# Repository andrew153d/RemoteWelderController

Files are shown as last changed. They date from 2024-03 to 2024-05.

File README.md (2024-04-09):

# RemoteWelderController #

A pair of devices meant to retrofit older welders with wireless connectivity. This document covers the usage and mechanical makeup, the cost overview can be found [here](https://github.com/andrew153d/RemoteWelderController/tree/main/hardware). There is also a preview of the site at this [link](https://andrew153d.github.io/RemoteWelderController/firmware/webpage/web_controller.html), note functionality is limited.

--- 

<p align="center">
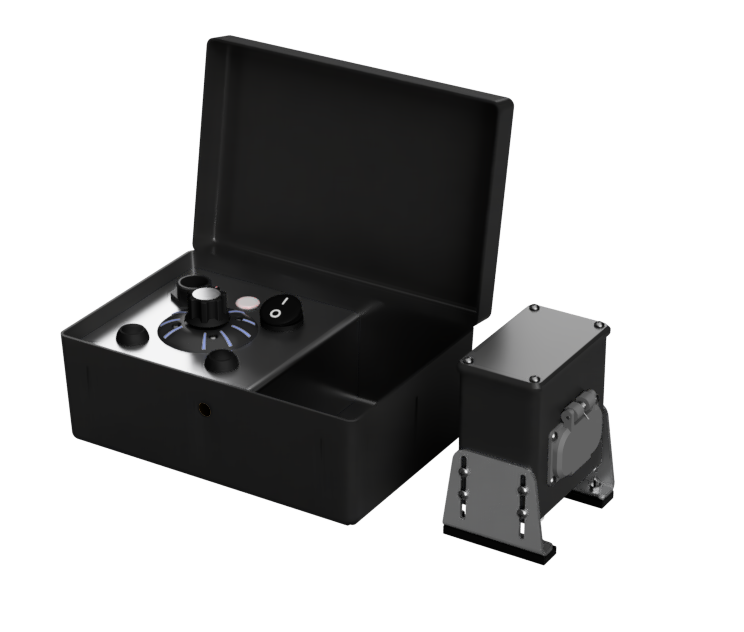
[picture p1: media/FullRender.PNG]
Pelican Render

</p>        

## Usage

There are three main modes of operation: Standard, Web Control, and Extended Web Control

### Standard Control

To enter standard control mode, toggle the Transmitter power switch to the 'ON' position and press the Power button on the Receiver. While the devices are searching for each other, their status LEDs will flash blue and will transition to solid green when connected. Rotation input on the control knob will result in proportional motion on the output shaft of the receiver. 

### Web Control

Web Control Mode will allow the user to make use of the web interface to control the output of the receiver. Press the power button on the receiver to turn the device on. After the status LED flashes blue, hold the power button for 3 seconds or until the LED turns to solid green. Connect your phone to the wifi network named Weld_---, open a browser and go to 'Weld.local'.

### Extended Web Control

Extended Web Control uses the Transmitter to host the webpage and repeats control to the receiver. After turning on both devices, hold both the up and down buttons for 3 seconds until the status LED turns green. Connect your phone to the Wifi network named Weld_--- and open the site 'Weld.Local'. In order to increase the usable distance, place the transmitter between the user and the receiver.

## Mechanical Details

### Web Interface 
<div align="center">
<p>
The webpage for control and configuration. Of course you can stay loyal to your brand while still bringing your welder into the modern world. The dial can be dragged to rotate, or the user can swipe the arrows at the bottom to rotate the knob. The lock button will match rotation on the output to the knob on the webpage. The align button will automatically measure the range of the output and scale the input accordingly. Settings and more configuration options can be accessed via the menu on the top left. 
</p>
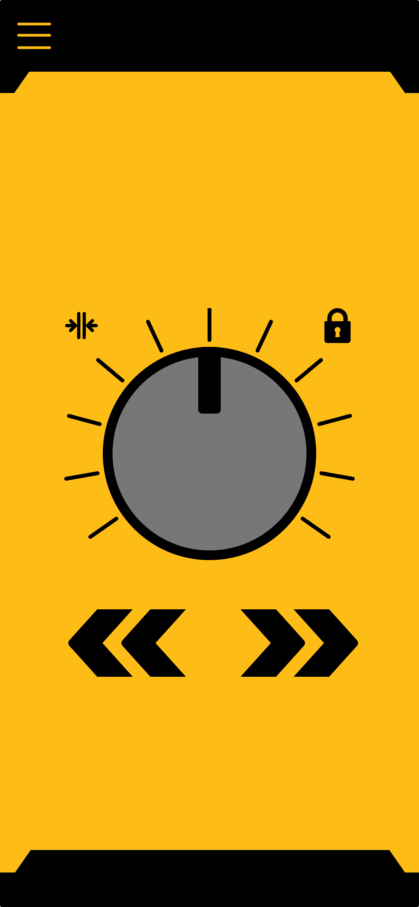
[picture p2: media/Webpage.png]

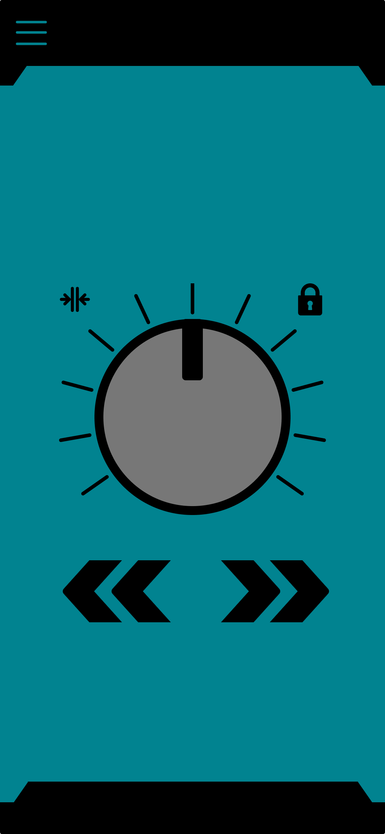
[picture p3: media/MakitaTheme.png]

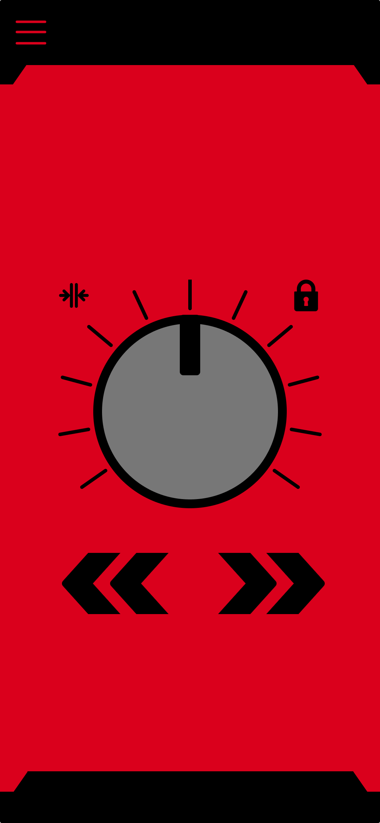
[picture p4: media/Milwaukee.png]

</div>

### Transmitter

<div align="center">
<p>
Top view of the pelican case with reciever stowed on the right side.
</p>
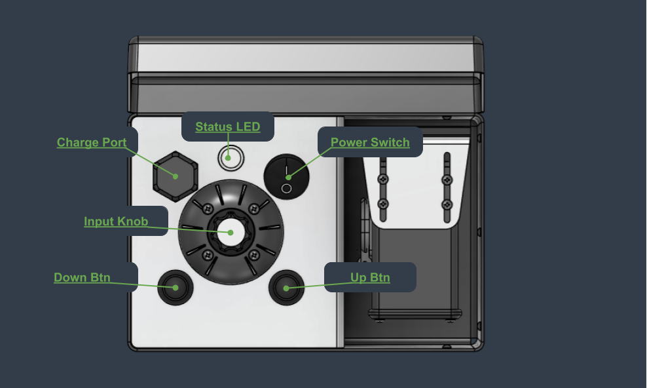
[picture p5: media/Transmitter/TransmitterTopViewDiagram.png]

</div>

<div align="center">

<p style="margin:0px 100px;">
The charge port cap can be removed to expose the USBC port and charge the device.
</p>
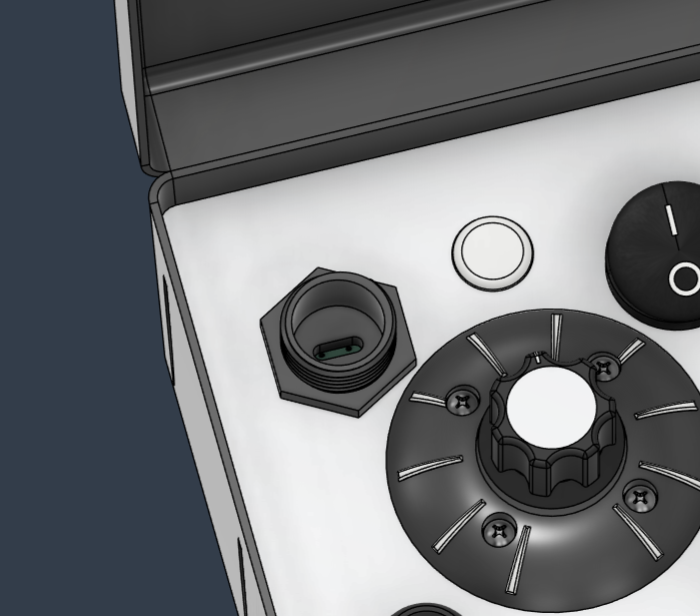
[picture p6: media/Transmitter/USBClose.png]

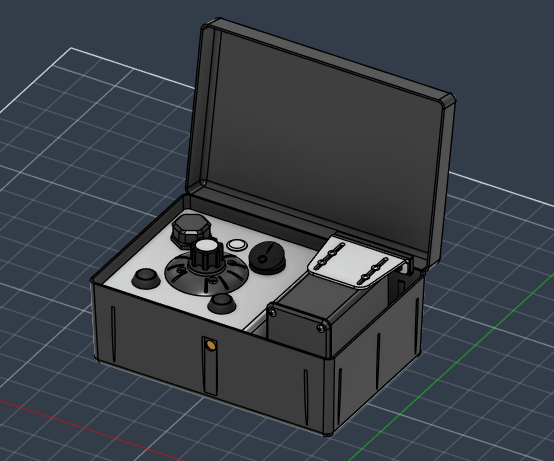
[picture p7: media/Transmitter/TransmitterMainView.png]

</div>

<div align="center">
<p style="margin:0px 100px;">
The circuit board and battery pack get mounted under the faceplate. Not shown is a cover to shield the electronics from debris under the faceplate.
</p>
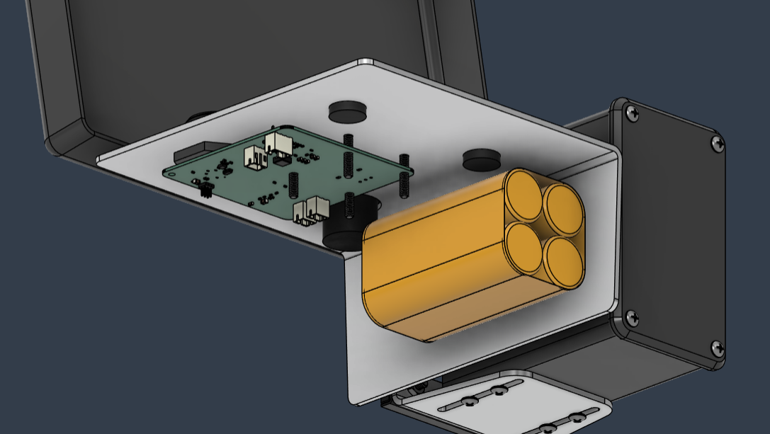
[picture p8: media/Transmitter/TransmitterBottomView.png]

</div>

### Receiver

<div align="center">
    <p>
        Receiver is shown without belt mechanism. The hatch is biased closed by a torsion spring and sealed against the surface with a O-ring.
    </p>
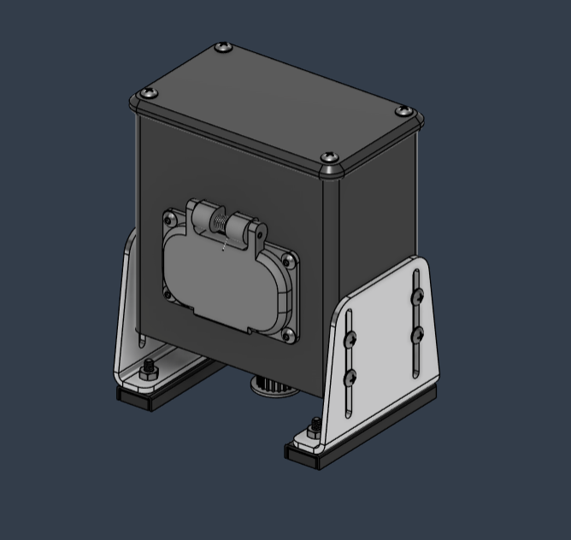
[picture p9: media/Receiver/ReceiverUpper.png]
    
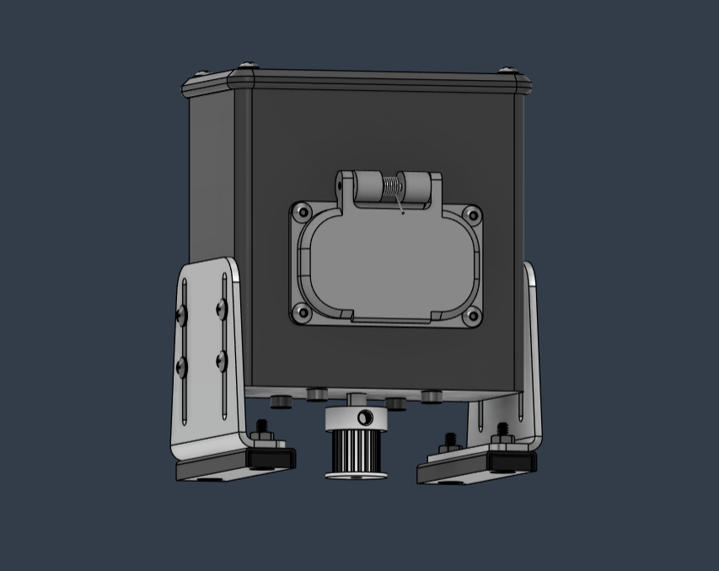
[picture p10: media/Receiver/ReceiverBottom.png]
Bottom View
    
</div>
<div align="center">
    <p>
    Shown below is the hatch on the receiver that exposes the charging port, status led, and power button. The power button serves multiple alternative functions described in the usage section.
    </p>
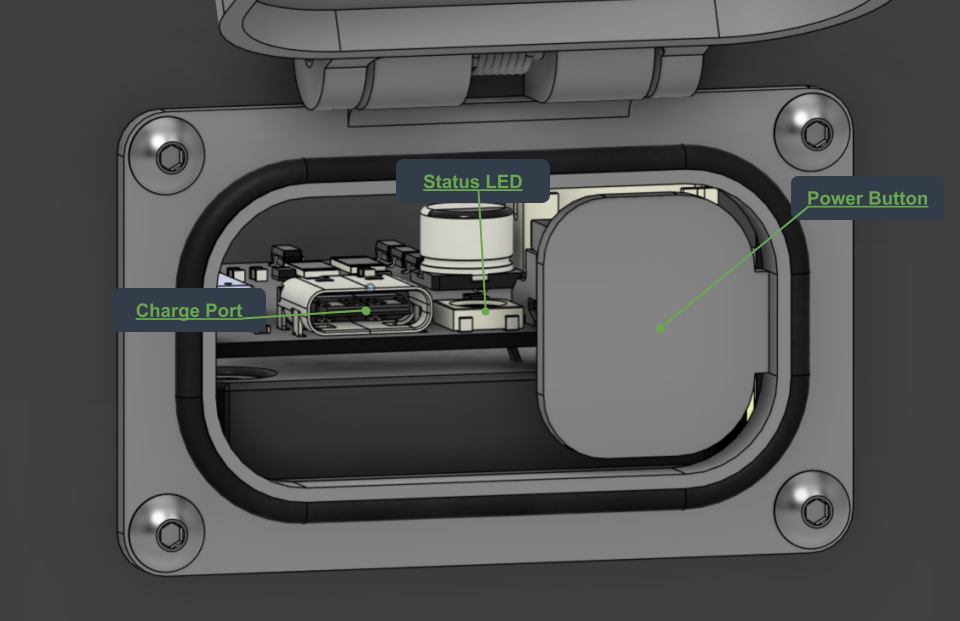
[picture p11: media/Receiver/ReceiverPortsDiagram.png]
    
</div>
<div align="center">
    <p>
    There are several seals on the receiver that maintain water resistance. The upper seal gets compressed between the upper cover and the case. There is also a seal on the access hatch as well as around the motor shaft.
    </p>
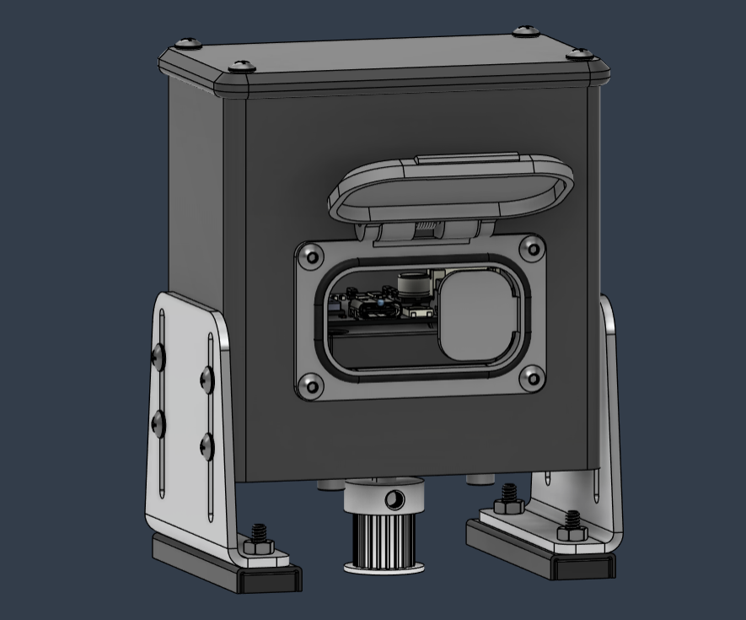
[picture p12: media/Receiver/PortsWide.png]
    
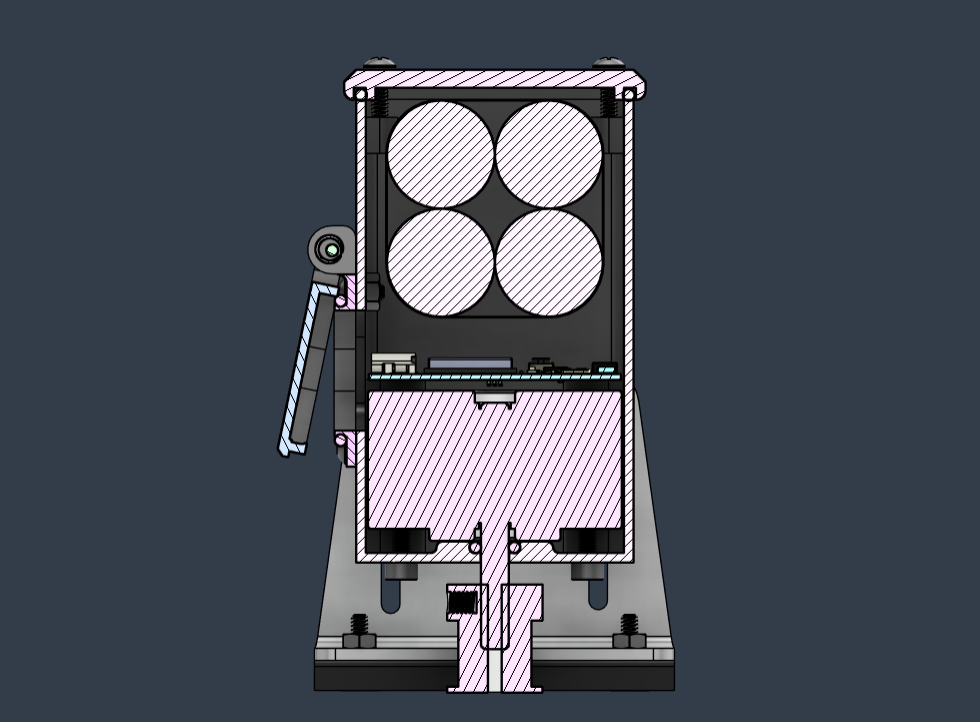
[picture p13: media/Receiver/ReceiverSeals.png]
    
</div>

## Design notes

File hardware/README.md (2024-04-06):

# BOM Overview and Cost #
This table is based on building 5 receivers and 5 transmitters. The total cost to build comes to $1050 and the individual cost to build of $210. Assuming four are sold at $300, the venture would profit $150.
## Transmitter ##

### Hardware Components ###

| Item | QT per device | Total QT | Cost per device | Total Cost | Purchase QT | Purchase Cost |
|---|---|---|---|---|---|---|
| [Pelican Case](https://www.pelican.com/us/en/product/cases/protector/1120?sku=1120-000-110) | 1 | 5 | $45.00 | $225 | 5 | $225 |
| [Momentary Switches](https://a.co/d/eoz4Ket) | 2 | 10 | $1.5 | $15.00 | 12 | $18.00 |
| [Power Switch](https://a.co/d/50zdfZq) | 1 | 5 | $0.89 | $4.5 | 10 | $9.00 |
| Aluminum Face Plate | 1| 5 | $14.33 | $40.00 | 5 | $40.00 |
| [Knob](https://www.mcmaster.com/6094K42)| 1 | 5 | $5.28 | $26.40 | 5 | $28.00 |

## Receiver ##

### Hardware Components ###

| Item | QT per device | Total QT | Cost per unit | Total Cost | Purchase QT | Purchase Cost |
|-|-|-|-|-|-|-|
| [Stepper](https://www.omc-stepperonline.com/e-series-nema-17-bipolar-1-8deg-17ncm-24-07oz-in-1a-42x42x23mm-4-wires-17he08-1004s)  | 1 | 5 | $4.26 | $21.30 | 5 | $25.00 |
| [Magnet Mounting Screws](https://www.mcmaster.com/catalog/130/3471/91772A107) | 4 | 20 | - | - | 100 | $6.50 |
| [Side Plate Mounting Screws](https://www.mcmaster.com/catalog/130/3432/91306A311) | 8 | 40 | - | - | 50 | 11.58 |
| [Magnets](https://a.co/d/8Z8Zce8)  | 2 | 10 | $2.12 | $22.00 | 12 | $26.00 |
| [Screws for feet](https://www.mcmaster.com/catalog/130/3471/91253A110) | 4 | 20 | - | - | 100 | 12.27 |
| [Upper O-Ring](https://www.mcmaster.com/1302N07/)| 1 | 5 | - | - | 25 | $12.03 |
| [Hatch O-Ring](https://www.mcmaster.com/1302N07/)| 1 | 5 | - | - | 25 | $12.03 |
| [Torsion Spring](https://www.mcmaster.com/9271K599)| 1 | 5 | - | - | 6 | $5.76 |
| Alumnium Legs | 1 | 5 | $2.38 | $20.38 | 10 | $23.00 |

## Common ##
| Item | QT per pair | Total QT | Cost per unit | Total Cost | Purchase QT | Purchase Cost |
|---|---|---|---|---|---|---|
| [18650 Batteries](https://www.18650batterystore.com/products/samsung-25r-18650) | 8 | 40 | $3.75 | $150 | 40 | $170 |
| [JST connector Pack](https://a.co/d/7OMg5ZO) | - | - | - | - | 1 | $26.00 |
| [Spot Welder](https://a.co/d/g4Re4Je) | - | - | - | - | 1 | $68.00 | 
| Misc wire | - | - | - | - | 1 | $20.00 |
| [Conformal Coating](https://a.co/d/c47sdoQ) | - | - | - | - | - | $35.44
| [Heat Shrink](https://a.co/d/8j2zc0W) | - | - | - | - | - | $10.00

### PCB Components ###
| Item/PN | QT per device | Total QT | Cost per unit | Total Cost | Purchase QT | Purchase Cost |
|---|---|---|---|---|---|---|
| All Components | alot | alot | 50 | 250 | alot | 250 |

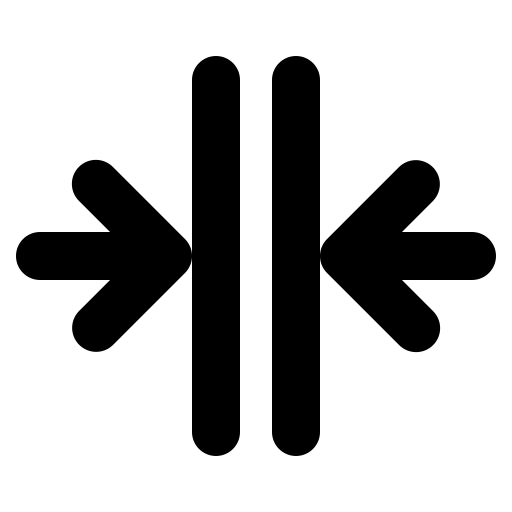
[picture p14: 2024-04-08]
media/merge.png

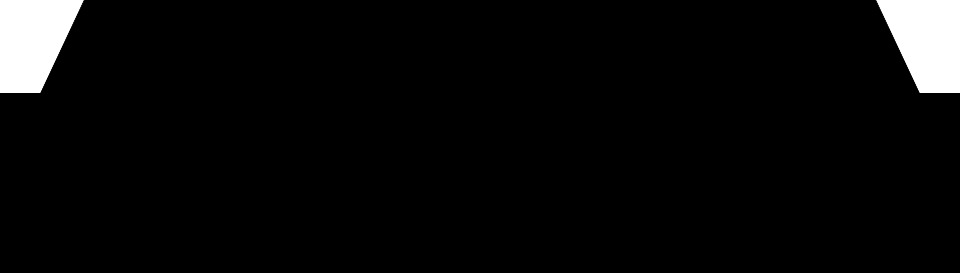
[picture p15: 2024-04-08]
media/Bottom Border.png

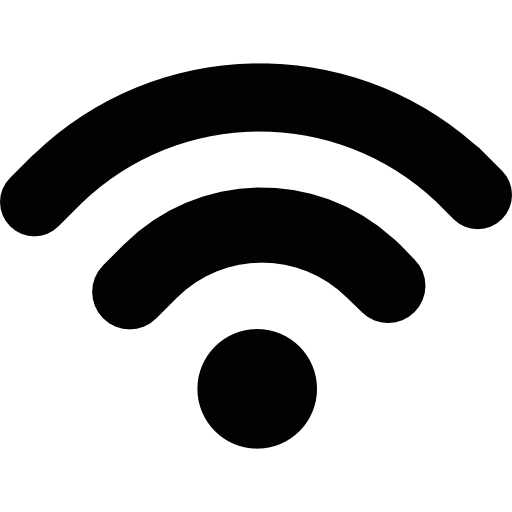
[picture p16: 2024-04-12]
media/wi-fi.png

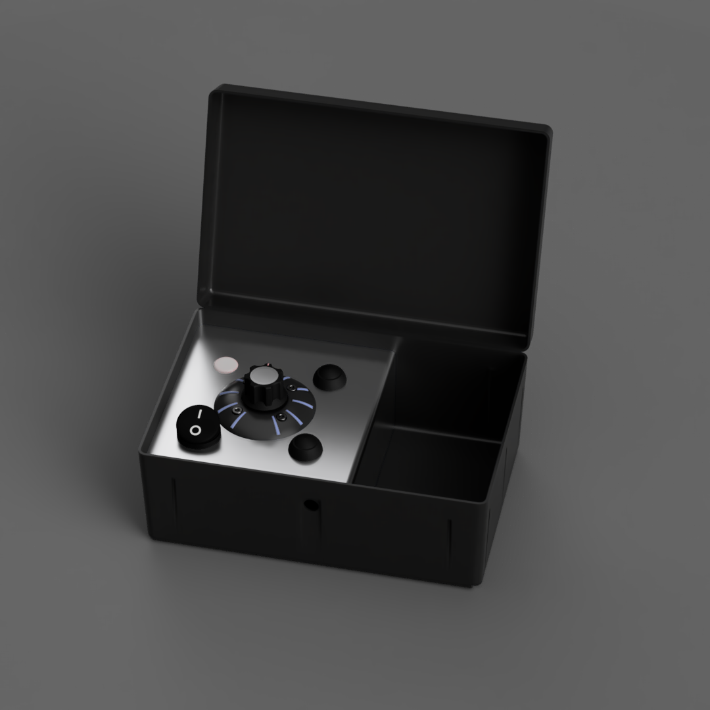
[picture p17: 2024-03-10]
media/Transmitter/PelicanRender.png

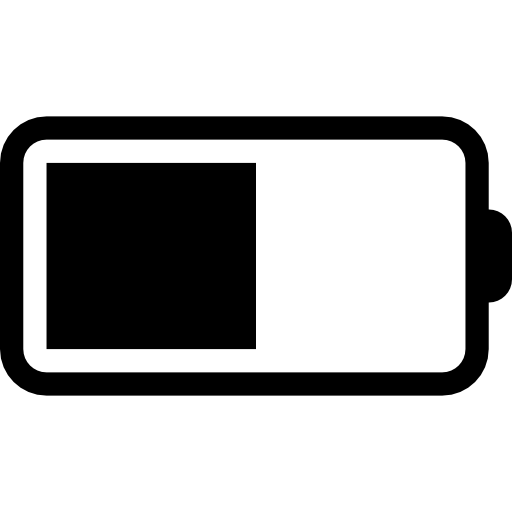
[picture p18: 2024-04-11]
media/battery.png

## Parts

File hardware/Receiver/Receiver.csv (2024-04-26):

Order Status | Reference | Qty | Value | Footprint | DNP
 | A1 | 1 | ~ | Package_DFN_QFN:QFN-28_4x4mm_P0.5mm
 | BQ25792RQMR1 | 1 | ~ | Lipo_Charger:BQ25792
 | BT1, BT2, BT3, BT4 | 4 | Battery_Cell
 | C1, C11, C29, C31, C35, C36, C39, C40, C44, C45, C47 | 11 | 0.1u | Capacitor_SMD:C_0402_1005Metric
 | C2, C3, C6, C8, C10, C12, C13, C15, C16, C17, C18, C19, C20, C26, C33, C34 | 16 | 10u | Capacitor_SMD:C_0603_1608Metric
 | C4, C5 | 2 | 47n | Capacitor_SMD:C_0402_1005Metric
 | C7 | 1 | .1u | Capacitor_SMD:C_0402_1005Metric
 | C9 | 1 | 4.7u | Capacitor_SMD:C_0402_1005Metric
 | C14 | 1 | NP | Capacitor_SMD:C_0402_1005Metric
 | C21, C22, C23, C24, C25 | 5 | 220nf | Capacitor_SMD:C_0402_1005Metric
 | C27, C30, C32, C38 | 4 | 1u | Capacitor_SMD:C_0402_1005Metric
 | C28 | 1 | 100p | Capacitor_SMD:C_0402_1005Metric
 | C37, C46 | 2 | 22u | Capacitor_SMD:C_0805_2012Metric
 | C41 | 1 | 47u | Capacitor_SMD:CP_Elec_6.3x5.4
 | C42, C43 | 2 | 0.22u | Capacitor_SMD:C_0402_1005Metric
 | D1 | 1 | LED | LED_SMD:LED_0603_1608Metric
 | D2 | 1 | LED | Capacitor_SMD:C_0805_2012Metric
 | D3 | 1 | WS2812B | LED_SMD:LED_WS2812B_PLCC4_5.0x5.0mm_P3.2mm
 | D4, D7, D8, D9, D10 | 5 | 1N4148WQ-13-F | Diode_SMD:D_SOD-123
 | D5 | 1 | D_Zener | Diode_SMD:D_SOD-323F
 | D6 | 1 | EVVO SS16 | Diode_SMD:D_SMA
 | D11, D12, D13 | 3 | ESD051-1F4 | Diode_SMD:D_0201_0603Metric
 | H1, H2, H3, H4 | 4 | MountingHole | MountingHole:MountingHole_3.2mm_M3_DIN965_Pad_TopBottom
 | J1 | 1 | USB_C_Receptacle_USB2.0 | Connector_USB:USB_C_Receptacle_JAE_DX07S016JA1R1500
 | J2 | 1 | 20021511-00006T4LF
 | J3 | 1 | JST_PH | Connector_JST:JST_PH_B6B-PH-K_1x06_P2.00mm_Vertical
 | J4 | 1 | Conn_01x04 | Connector_JST:JST_PH_B4B-PH-K_1x04_P2.00mm_Vertical
 | JP1 | 1 | BQ76905_Bypass | Jumper:SolderJumper-2_P1.3mm_Open_RoundedPad1.0x1.5mm
 | L1 | 1 | 1u | Inductor_SMD:L_Sunlord_MWSA0402S
 | Q1 | 1 | 2N7002 | Package_TO_SOT_SMD:SOT-23
 | Q2, Q3 | 2 | NMOS | Package_TO_SOT_SMD:SOT-23
 | Q4 | 1 | PMOS | Package_TO_SOT_SMD:SOT-23
 | R1, R2, R16, R34, R35, R36, R38, R41 | 8 | 10k | Resistor_SMD:R_0402_1005Metric
 | R3, R4, R5 | 3 | 5.1k | Capacitor_SMD:C_0402_1005Metric
 | R6, R31, R32 | 3 | 5.1k | Resistor_SMD:R_0402_1005Metric
 | R7, R9, R11, R17, R18, R19, R20, R33, R39, R42 | 10 | 100k | Resistor_SMD:R_0402_1005Metric
 | R8 | 1 | 1M | Resistor_SMD:R_0402_1005Metric
 | R10, R26, R28, R29 | 4 | 100 | Resistor_SMD:R_0402_1005Metric
 | R12 | 1 | 127k | Resistor_SMD:R_0402_1005Metric
 | R13 | 1 | 5.24k | Resistor_SMD:R_0402_1005Metric
 | R14 | 1 | 30.31k | Resistor_SMD:R_0402_1005Metric
 | R15 | 1 | 6.04k | Resistor_SMD:R_0402_1005Metric
 | R21, R22, R23, R24, R25 | 5 | 10 | Resistor_SMD:R_0402_1005Metric
 | R27 | 1 | 1m | Resistor_SMD:R_0402_1005Metric
 | R30 | 1 | 0 | Resistor_SMD:R_0402_1005Metric
 | R37 | 1 | NP | Resistor_SMD:R_0402_1005Metric
 | R40 | 1 | 20k | Resistor_SMD:R_0402_1005Metric
 | R43, R44 | 2 | 68m | Resistor_SMD:R_0402_1005Metric
 | SW1 | 1 | Reset | Switch:Tactile_5.5mmx2.85mm
 | SW2 | 1 | Boot | Switch:Tactile_5.5mmx2.85mm
 | SW3 | 1 | 1825027-8 | Button_THT:SW2_1825027-C_TEC
 | U1, U5 | 2 | TPS22810DRV | Package_SON:WSON-6-1EP_2x2mm_P0.65mm_EP1x1.6mm
 | U2, U3 | 2 | DMG6602SVTQ | Package_TO_SOT_SMD:TSOT-23-6
 | U4 | 1 | TLV493DA1B6HTSA2 | Package_TO_SOT_SMD:SOT-23-6
 | U6 | 1 | BQ76905 | Package_DFN_QFN:UQFN-20-1EP_3x3mm_P0.4mm_EP1.85x1.85mm
 | U7 | 1 | AZ1117-3.3 | Package_TO_SOT_SMD:SOT-223
 | U8 | 1 | ESP32-S3-MINI-1-N8 | XCVR_ESP32-S3-MINI-1-N8:XCVR_ESP32-S3-MINI-1-N8

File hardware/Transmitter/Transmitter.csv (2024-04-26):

Order Status | Reference | Qty | Value | Footprint | DNP
 | BQ25792RQMR1 | 1 | ~ | Lipo_Charger:BQ25792
 | BT1, BT2, BT3, BT4 | 4 | Battery_Cell
 | C1, C10, C23, C28, C36, C39, C40 | 7 | 0.1u | Capacitor_SMD:C_0402_1005Metric
 | C2, C5, C7, C9, C11, C12, C13, C14, C15, C17, C18, C19, C22 | 13 | 10u | Capacitor_SMD:C_0603_1608Metric
 | C3, C4 | 2 | 47n | Capacitor_SMD:C_0402_1005Metric
 | C6 | 1 | .1u | Capacitor_SMD:C_0402_1005Metric
 | C8 | 1 | 4.7u | Capacitor_SMD:C_0402_1005Metric
 | C16, C25 | 2 | 10u | Capacitor_SMD:C_0402_1005Metric
 | C20, C29, C37, C38 | 4 | 1u | Capacitor_SMD:C_0402_1005Metric
 | C21 | 1 | 1n | Capacitor_SMD:C_0402_1005Metric
 | C24 | 1 | 10uf | Capacitor_SMD:C_0402_1005Metric
 | C26 | 1 | 22u | Capacitor_SMD:C_0402_1005Metric
 | C27 | 1 | 22u | Capacitor_SMD:C_0805_2012Metric
 | C30, C31, C32, C33, C34 | 5 | 220nf | Capacitor_SMD:C_0402_1005Metric
 | C35 | 1 | 100p | Capacitor_SMD:C_0402_1005Metric
 | D1 | 1 | LED | LED_SMD:LED_0603_1608Metric
 | D2 | 1 | LED | Capacitor_SMD:C_0805_2012Metric
 | D3 | 1 | D_Schottky | Diode_SMD:D_SOD-128
 | D4 | 1 | D_Zener | Diode_SMD:D_SOD-323F
 | D5 | 1 | WS2812B | LED_SMD:LED_WS2812B_PLCC4_5.0x5.0mm_P3.2mm
 | D6, D7, D8, D9 | 4 | 1N4148WQ-13-F | Diode_SMD:D_SOD-123
 | H1, H2, H3, H4, H5 | 5 | MountingHole | MountingHole:MountingHole_3.2mm_M3_DIN965_Pad_TopBottom
 | J1 | 1 | USB_C_Receptacle_USB2.0 | footprints:CONN_GSB1CA11101DSHR_AMP
 | J2 | 1 | UP_BTN | Connector_JST:JST_PH_B2B-PH-K_1x02_P2.00mm_Vertical
 | J3 | 1 | DN_BTN | Connector_JST:JST_PH_B2B-PH-K_1x02_P2.00mm_Vertical
 | J4 | 1 | UART
 | J6 | 1 | JST_PH | Connector_JST:JST_PH_B6B-PH-K_1x06_P2.00mm_Vertical
 | JP1 | 1 | BQ76905_Bypass | Jumper:SolderJumper-2_P1.3mm_Open_RoundedPad1.0x1.5mm
 | L1 | 1 | 1u | Inductor_SMD:L_Sunlord_MWSA0402S
 | Q1 | 1 | 2N7002 | Package_TO_SOT_SMD:SOT-23
 | Q12, Q13 | 2 | NMOS | Package_TO_SOT_SMD:SOT-23
 | Q14 | 1 | PMOS | Package_TO_SOT_SMD:SOT-23
 | R1, R2, R16, R20 | 4 | 10k | Resistor_SMD:R_0402_1005Metric
 | R3, R4, R5 | 3 | 5.1k | Capacitor_SMD:C_0402_1005Metric
 | R6, R47, R48 | 3 | 5.1k | Resistor_SMD:R_0402_1005Metric
 | R7, R8, R9, R10 | 4 | 100k | Capacitor_SMD:C_0402_1005Metric
 | R11, R42, R44, R45 | 4 | 100 | Resistor_SMD:R_0402_1005Metric
 | R12 | 1 | 127k | Resistor_SMD:R_0402_1005Metric
 | R13 | 1 | 5.24k | Resistor_SMD:R_0402_1005Metric
 | R14 | 1 | 30.31k | Resistor_SMD:R_0402_1005Metric
 | R15 | 1 | 6.04k | Resistor_SMD:R_0402_1005Metric
 | R17, R49 | 2 | 100k | Resistor_SMD:R_0402_1005Metric
 | R18, R19 | 2 | 10k | Capacitor_SMD:C_0402_1005Metric
 | R37, R38, R39, R40, R41 | 5 | 10 | Resistor_SMD:R_0402_1005Metric
 | R43 | 1 | 1m | Resistor_SMD:R_0402_1005Metric
 | R46 | 1 | 0 | Resistor_SMD:R_0402_1005Metric
 | RV1 | 1 | R_Potentiometer | Potentiometer_THT:Potentiometer_Alps_RK09L_Single_Vertical
 | SW1 | 1 | Reset | Switch:Tactile_5.5mmx2.85mm
 | SW2 | 1 | SW_SPST | Connector_JST:JST_PH_B2B-PH-K_1x02_P2.00mm_Vertical
 | SW3 | 1 | Boot | Switch:Tactile_5.5mmx2.85mm
 | U1, U2 | 2 | TPS22810DRV | Package_SON:WSON-6-1EP_2x2mm_P0.65mm_EP1x1.6mm
 | U3 | 1 | AZ1117-3.3 | AZ1117:SOT223
 | U4 | 1 | ESP32-S3-MINI-1-N8 | XCVR_ESP32-S3-MINI-1-N8:XCVR_ESP32-S3-MINI-1-N8
 | U5 | 1 | ~ | Package_DFN_QFN:UQFN-20-1EP_3x3mm_P0.4mm_EP1.85x1.85mm

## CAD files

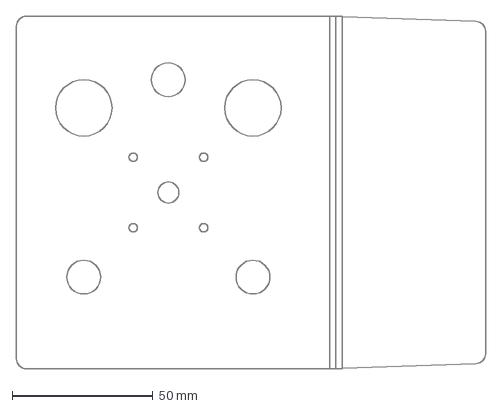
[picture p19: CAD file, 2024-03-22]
models/Transmitter/Main Plate.dxf
166.4 x 125.1 mm

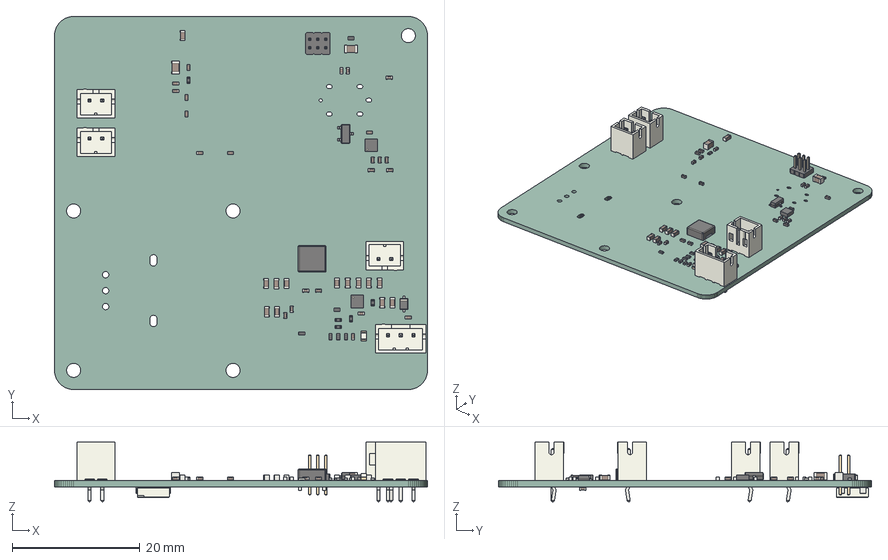
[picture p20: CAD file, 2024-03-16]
hardware/Transmitter/Transmitter.step
58.5 x 58.5 x 9.40 mm
Transmitter PCB

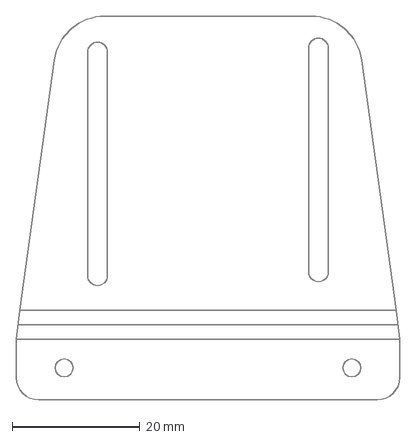
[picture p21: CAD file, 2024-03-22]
models/Receiver/Receiver Side Plate.dxf
60.0 x 60.1 mm

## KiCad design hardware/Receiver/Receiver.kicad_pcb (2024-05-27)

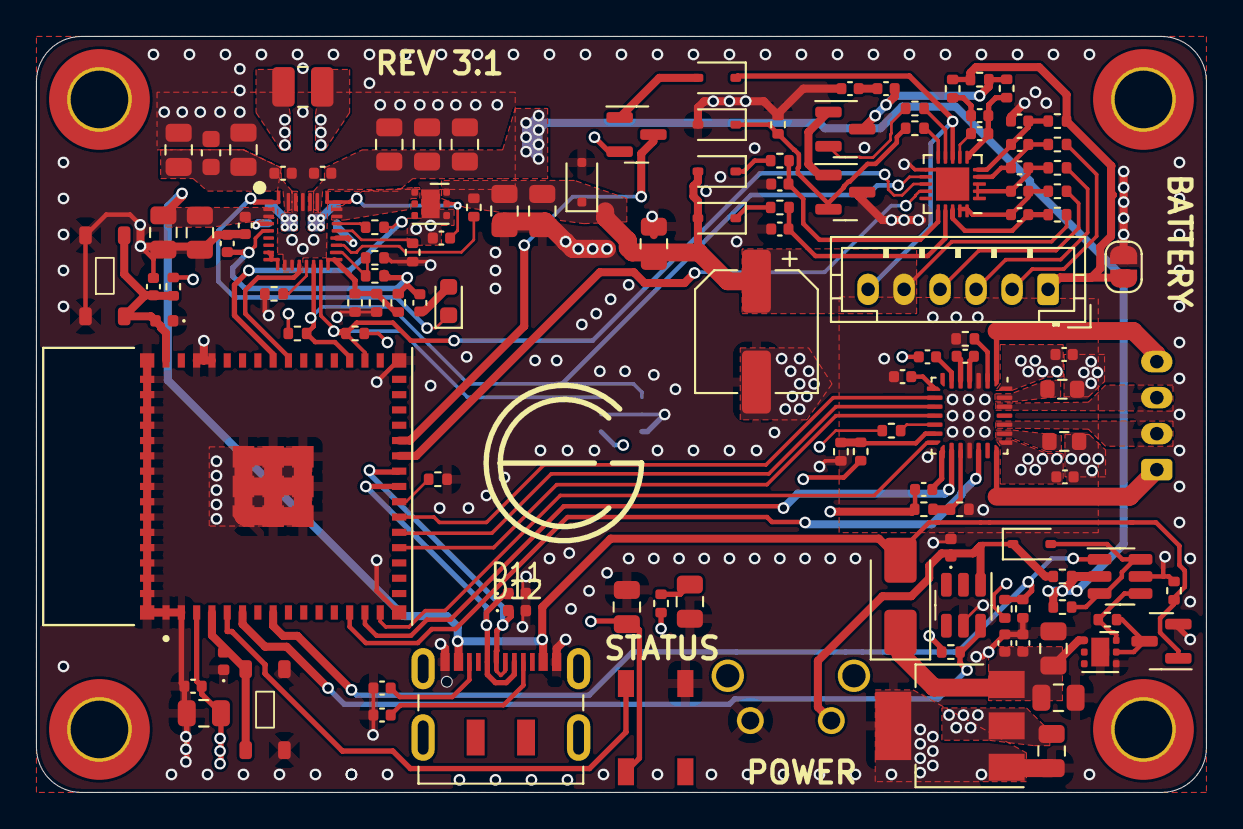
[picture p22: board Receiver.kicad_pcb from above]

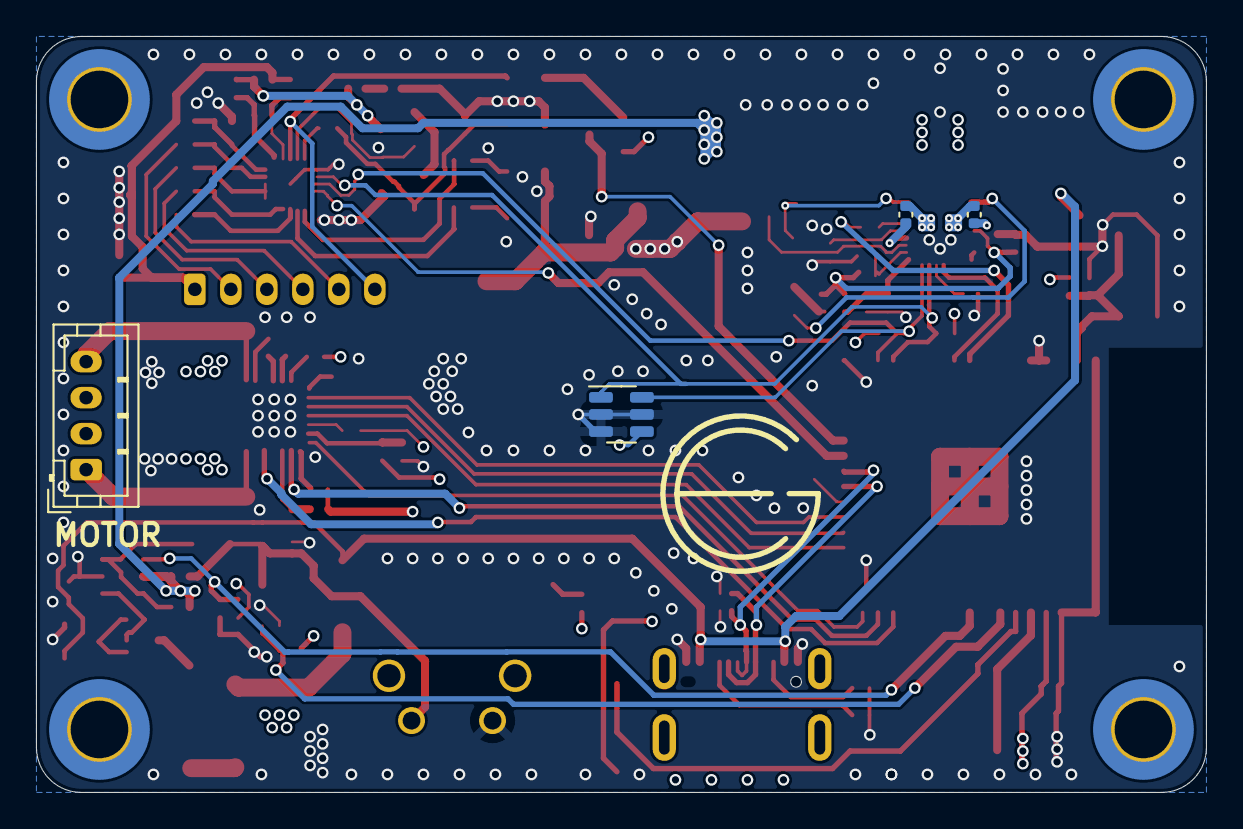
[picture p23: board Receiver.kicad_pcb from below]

Board: 4 copper layers, 65.0 x 42.0 mm, 131 parts (4 on the bottom side), 89 nets.

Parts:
A1: QFN-28_4x4mm_P0.5mm
BQ25792RQMR1: BQ25792
C1, C11, C29, C31, C35, C36, C39, C40, C44, C45, C47: 0.1u; C_0402_1005Metric
C2, C3, C6, C10, C12, C13, C15, C16, C17, C18, C26, C33, C34: 10u; C_0805_2012Metric
C4, C5: 47n; C_0402_1005Metric
C7: .1u; C_0402_1005Metric
C8: 10u; C_0603_1608Metric
C9: 4.7u; C_0402_1005Metric
C14: NP; C_0402_1005Metric
C21, C22, C23, C24, C25: 220nf; C_0402_1005Metric
C27, C30, C32, C38: 1u; C_0402_1005Metric
C28: 100p; C_0402_1005Metric
C37, C46: 22u; C_0805_2012Metric
C41: 47u; CP_Elec_6.3x5.4
C42, C43: 0.22u; C_0402_1005Metric
D1: LED; LED_0603_1608Metric
D2: LED; C_0805_2012Metric
D3: WS2812B; LED_WS2812B_PLCC4_5.0x5.0mm_P3.2mm
D4, D7, D8, D9, D10: 1N4148WQ-13-F; D_SOD-323
D5: D_Zener; D_SOD-323F
D6: EVVO SS16; D_SMA
D11, D12, D13, D14, D15: TVN3V3B1S; D_0402_1005Metric
H1, H2, H3, H4: MountingHole; MountingHole_3.2mm_M3_DIN965_Pad_TopBottom
J1: USB_C_Receptacle_USB2.0; USB_C_Receptacle_JAE_DX07S016JA1R1500
J3: JST_PH; JST_PH_B6B-PH-K_1x06_P2.00mm_Vertical
J4: Conn_01x04; JST_PH_B4B-PH-K_1x04_P2.00mm_Vertical
JP1: BQ76905_Bypass; SolderJumper-2_P1.3mm_Open_RoundedPad1.0x1.5mm
L1: 1u; L_1008_2520Metric
Q1: 2N7002; SOT-23
Q2, Q3: NMOS; SOT-23
Q4: PMOS; SOT-23
R1, R2, R16, R34, R35, R36, R38, R41, R45: 10k; R_0402_1005Metric
R3, R4, R5: 5.1k; C_0402_1005Metric
R6, R31, R32: 5.1k; R_0402_1005Metric
R7, R9, R11, R17, R18, R19, R20, R33, R39, R42: 100k; R_0402_1005Metric
R8: 1M; R_0402_1005Metric
R10, R26, R28, R29: 100; R_0402_1005Metric
R12: 127k; R_0402_1005Metric
R13: 5.24k; R_0402_1005Metric
R14: 30.31k; R_0402_1005Metric
R15: 6.04k; R_0402_1005Metric
R21, R22, R23, R24, R25: 10; R_0402_1005Metric
R27: 1m; R_0402_1005Metric
R30: 0; R_0402_1005Metric
R37: NP; R_0402_1005Metric
R40: 20k; R_0402_1005Metric
R43, R44: 68m; R_0603_1608Metric
SW1: Reset; Tactile_5.5mmx2.85mm
SW2: Boot; Tactile_5.5mmx2.85mm
SW3: 1825027-8; SW2_1825027-C_TEC
U1, U5: TPS22810DRV; WSON-6-1EP_2x2mm_P0.65mm_EP1x1.6mm
U2, U3: DMG6602SVTQ; TSOT-23-6
U4: TLV493DA1B6HTSA2; SOT-23-6
U6: BQ76905; UQFN-20-1EP_3x3mm_P0.4mm_EP1.85x1.85mm
U7: AZ1117-3.3; SOT-223
U8: ESP32-S3-MINI-1-N8; XCVR_ESP32-S3-MINI-1-N8

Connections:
+3.3V: C6.1, C37.1, C42.1, C44.1, C46.1, D3.1 (VDD), Q4.2 (G), R6.1, R7.1, R11.1, R34.1, R35.1, R36.1, R37.1, R40.1, R42.1, U4.4 (VDD), U7.2 (VO), U8.3 (3V3)
/ADDRS_LED: D3.4 (DIN), U8.5 (IO1)
/ALERT: U6.14 (ALERT), U8.25 (IO21)
/BAT+: A1.22 (VBB1), A1.28 (VBB2), C16.1, C18.1, C34.1, C39.1, C40.1, C41.1, C45.1, D5.1 (K), D7.2 (A), D8.2 (A), J3.5, R10.2, R21.1, U1.6 (VIN)
/BATP: BQ25792RQMR1.18 (BATP), R10.1
/BAT_C0: J3.1, JP1.1 (A), R25.1, R26.2, R27.1
/BAT_C1: J3.2, R24.1
/BAT_C2: J3.3, R23.1
/BAT_C3: J3.4, R22.1
/BC_INT: R2.2, U8.38 (IO42/TMS)
/BTST1: BQ25792RQMR1.4 (BTST1), C4.1
/BTST2: BQ25792RQMR1.19 (BTST2), C5.2
/CE: BQ25792RQMR1.13 (CE), R1.1
/CNTRL: D4.2 (A), R17.1, U2.3 (G2), U2.6 (D1)
/D+: D12.1 (A1), J1.A6 (D+), J1.B6 (D+), U8.24 (IO20/D+)
/D-: D11.1 (A1), J1.A7 (D-), J1.B7 (D-), U8.23 (IO19/D-)
/DIR: A1.19 (DIR), U8.13 (IO9)
/ESP_EN: C38.1, D14.2 (A2), R36.2, SW1.2, U8.45 (EN)
/ESP_IO0: D15.2 (A2), SW2.2, U8.4 (IO0_BOOT0)
/ILIM_HIZ: BQ25792RQMR1.17 (ILIM_HIZ), R12.1, R18.1
/INT: BQ25792RQMR1.21 (INT), R2.1
/MOT_nSLEEP: A1.14 (nSLEEP), U8.15 (IO11)
/MS1: A1.9 (MS1), U8.21 (IO17/DAC1)
/MS2: A1.10 (MS2), U8.20 (IO16)
/MS3: A1.11 (MS3), U8.19 (IO15)
/OUT1A: A1.24 (OUT1A), J4.2
/OUT1B: A1.21 (OUT1B), J4.1
/OUT2A: A1.26 (OUT2A), J4.3
/OUT2B: A1.1 (OUT2B), J4.4
/PMID: BQ25792RQMR1.29 (PMID), C7.1, C8.1, C10.1, C12.1
/PROG: BQ25792RQMR1.20 (PROG), R15.1
/QON: BQ25792RQMR1.12 (nQON), U8.37 (IO41/TDI)
/REGN: BQ25792RQMR1.5 (REGN), C9.1, R3.1, R12.2, R13.1
/ROSC: A1.13 (ROSC), R37.2, R38.1
/SCL: BQ25792RQMR1.14 (SCL), R35.2, U4.1 (SCL/INT), U6.12 (SCL), U8.33 (IO37)
/SDA: BQ25792RQMR1.15 (SDA), R34.2, U4.6 (SDA/ADDR), U6.13 (SDA), U8.32 (IO36)
/SDRV: BQ25792RQMR1.24 (SDRV), C14.1, U1.5 (EN/UVLO)
/SHUTDOWN: R7.2, R8.1, U2.1 (G1), U8.8 (IO4)
/STAT: BQ25792RQMR1.1 (STAT), D1.1 (K)
/STEP: A1.16 (STEP), U8.14 (IO10)
/SW: R11.2, U3.6 (D1), U8.6 (IO2)
/SW1: BQ25792RQMR1.28 (SW1), C4.2, L1.2
/SW2: BQ25792RQMR1.26 (SW2), C5.1, L1.1
/TS: D9.1 (K), J3.6, U6.8 (TS)
/VAC: BQ25792RQMR1.8 (VAC2), BQ25792RQMR1.9 (VAC1)
/VBAT: BQ25792RQMR1.22 (BAT), BQ25792RQMR1.23 (BAT), U1.1 (VOUT)
/VC0: C24.2, C25.1, R25.2, U6.5 (VC0)
/VC1: C23.2, C24.1, R24.2, U6.4 (VC1)
/VC2: C22.2, C23.1, R23.2, U6.1 (VC3A), U6.2 (VC3B), U6.3 (VC2)
/VC3: C21.2, C22.1, R22.2, U6.19 (VC4A), U6.20 (VC4B)
/VC4: C21.1, R21.2, U6.18 (VC5)
/VCP: A1.6 (VCP), C45.2
/VIN: C26.1, C27.1, C31.1, C33.1, D6.1 (K), U5.1 (VOUT), U7.3 (VI)
/VREF: A1.17 (REF), R40.2, R41.1
/VSYS: BQ25792RQMR1.25 (SYS), C11.1, C13.1, C15.1, C17.1, R9.1, R17.2, U2.2 (S2)
/VUSB: BQ25792RQMR1.2 (VBUS), BQ25792RQMR1.3 (VBUS), C1.1, C2.1, C3.1, D6.2 (A), J1.A4 (VBUS), J1.A9 (VBUS), J1.B4 (VBUS), J1.B9 (VBUS), Q1.1 (G), R19.1
/WAKE: Q4.3 (S), U8.26 (IO26)
GND: A1.3 (GND), A1.18 (GND), BQ25792RQMR1.10 (ACDRV2), BQ25792RQMR1.11 (ACDRV1), BQ25792RQMR1.27 (GND), C1.2, C2.2, C3.2, C6.2, C7.2, C8.2, C9.2, C10.2, C11.2, C12.2, C13.2, C14.2, C15.2, C16.2, C17.2, C18.2, C25.2, C26.2, C27.2, C30.2, C31.2, C32.2, C33.2, C34.2, C36.2, C37.2, C38.2, C39.2, C40.2, C41.2, C43.1, C44.2, C46.2, D2.1 (K), D3.3 (VSS), D5.2 (A), D10.2 (A), D11.2 (A2), D12.2 (A2), D13.2 (A2), D14.1 (A1), D15.1 (A1), J1.A1 (GND), J1.A12 (GND), J1.B1 (GND), J1.B12 (GND), JP1.2 (B), Q1.2 (S), Q3.3 (S), R1.2, R4.2, R5.2, R8.2, R14.2, R15.2, R16.2, R18.2, R19.2, R33.1, R38.2, R39.2, R41.2, R43.2, R44.2, R45.1, SW1.1, SW2.1, SW3.1, U1.4 (GND), U1.7 (GND), U2.5 (S1), U3.5 (S1), U4.2 (GND), U4.3 (GND), U4.5 (GND), U5.4 (GND), U5.7 (GND), U6.11 (VSS), U6.21 (VSS), U7.1 (GND), U7.4 (GND), U8.1 (GND), U8.2 (GND), U8.42 (GND), U8.43 (GND), U8.46 (GND), U8.47 (GND), U8.48 (GND), U8.49 (GND), U8.50 (GND), U8.51 (GND), U8.52 (GND), U8.53 (GND), U8.54 (GND), U8.55 (GND), U8.56 (GND), U8.57 (GND), U8.58 (GND), U8.59 (GND), U8.60 (GND), U8.61 (EXP), U8.62 (GND), U8.63 (GND), U8.64 (GND), U8.65 (GND)
unnamed: A1.4 (CP1), C47.1
unnamed: A1.5 (CP2), C47.2
unnamed: A1.23 (SENSE1), R43.1
unnamed: A1.27 (SENSE2), R44.1
unnamed: A1.15 (VDD), C42.2
unnamed: A1.8 (VREG), C43.2
unnamed: A1.2 (nEN), R39.1
unnamed: A1.12 (nRESET), R42.2
unnamed: BQ25792RQMR1.16 (TS), R13.2, R14.1, R16.1
unnamed: C35.2, C36.1
unnamed: D1.2 (A), R3.2
unnamed: D2.2 (A), R6.2
unnamed: D7.1 (K), R28.1
unnamed: D8.1 (K), R30.1
unnamed: D9.2 (A), Q4.1 (D)
unnamed: D10.1 (K), Q3.2 (G), R32.2, R33.2
unnamed: D4.1 (K), D13.1 (A1), R9.2, SW3.2, U3.1 (G1)
unnamed: J1.A5 (CC1), R4.1
unnamed: J1.B5 (CC2), R5.1
unnamed: Q1.3 (D), R20.1, U5.5 (EN/UVLO)
unnamed: Q2.1 (D), Q3.1 (D)
unnamed: Q2.2 (G), R31.2
unnamed: C35.1, Q2.3 (S), R27.2, R29.2
unnamed: R20.2, U2.4 (D2), U5.6 (VIN)
unnamed: C30.1, R28.2, U6.17 (BAT)
unnamed: R32.1, U6.10 (CHG)
unnamed: R31.1, U6.9 (DSG)
unnamed: C32.1, R30.2, U6.16 (REGSRC)
unnamed: C28.1, C29.1, R26.1, U6.7 (SRN)
unnamed: C28.2, C29.2, R29.1, U6.6 (SRP)
unnamed: R45.2, U8.22 (IO18/DAC2)

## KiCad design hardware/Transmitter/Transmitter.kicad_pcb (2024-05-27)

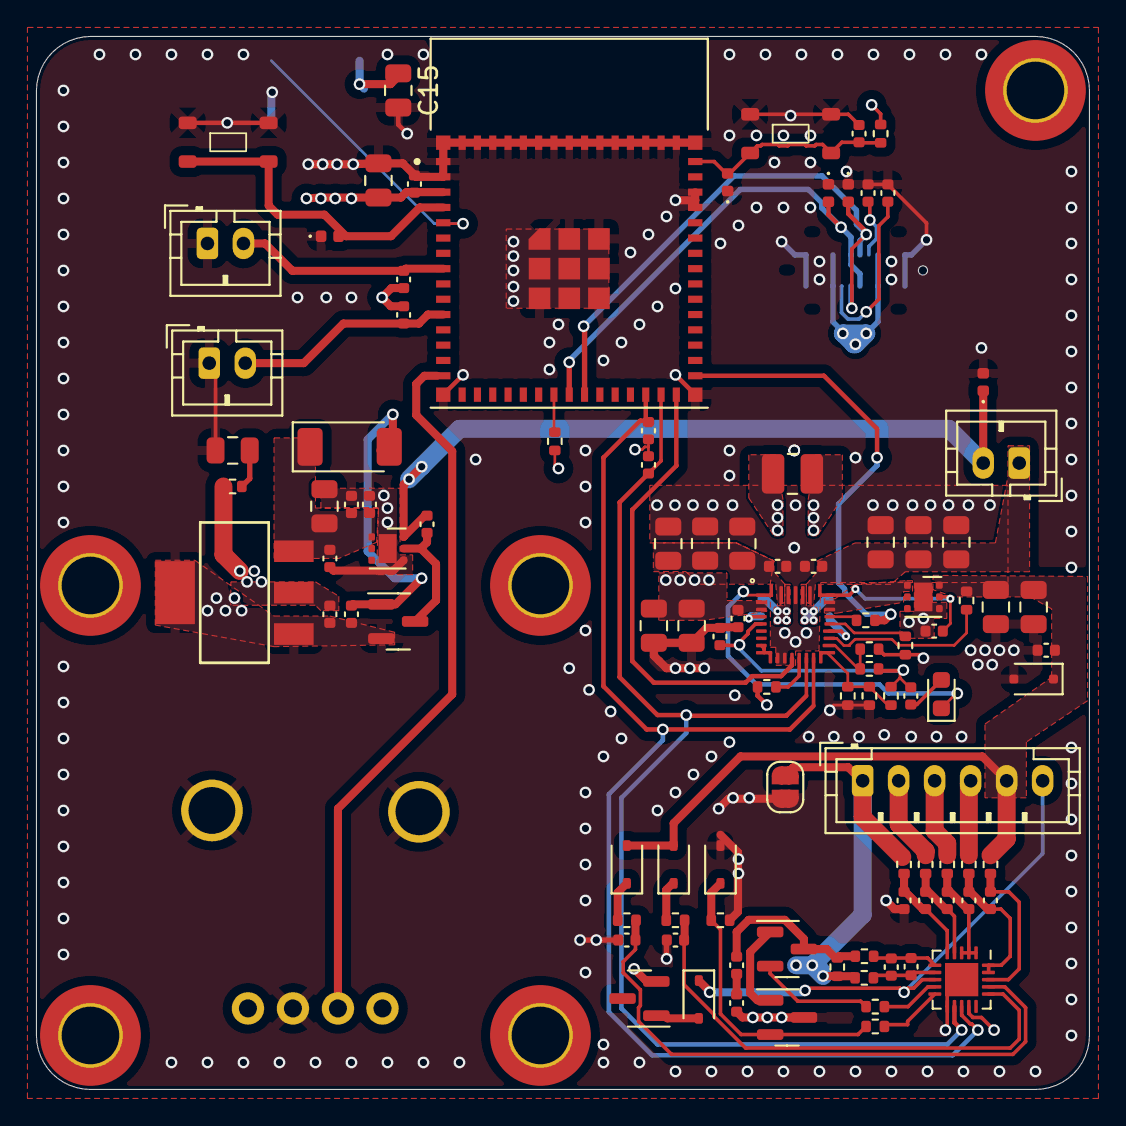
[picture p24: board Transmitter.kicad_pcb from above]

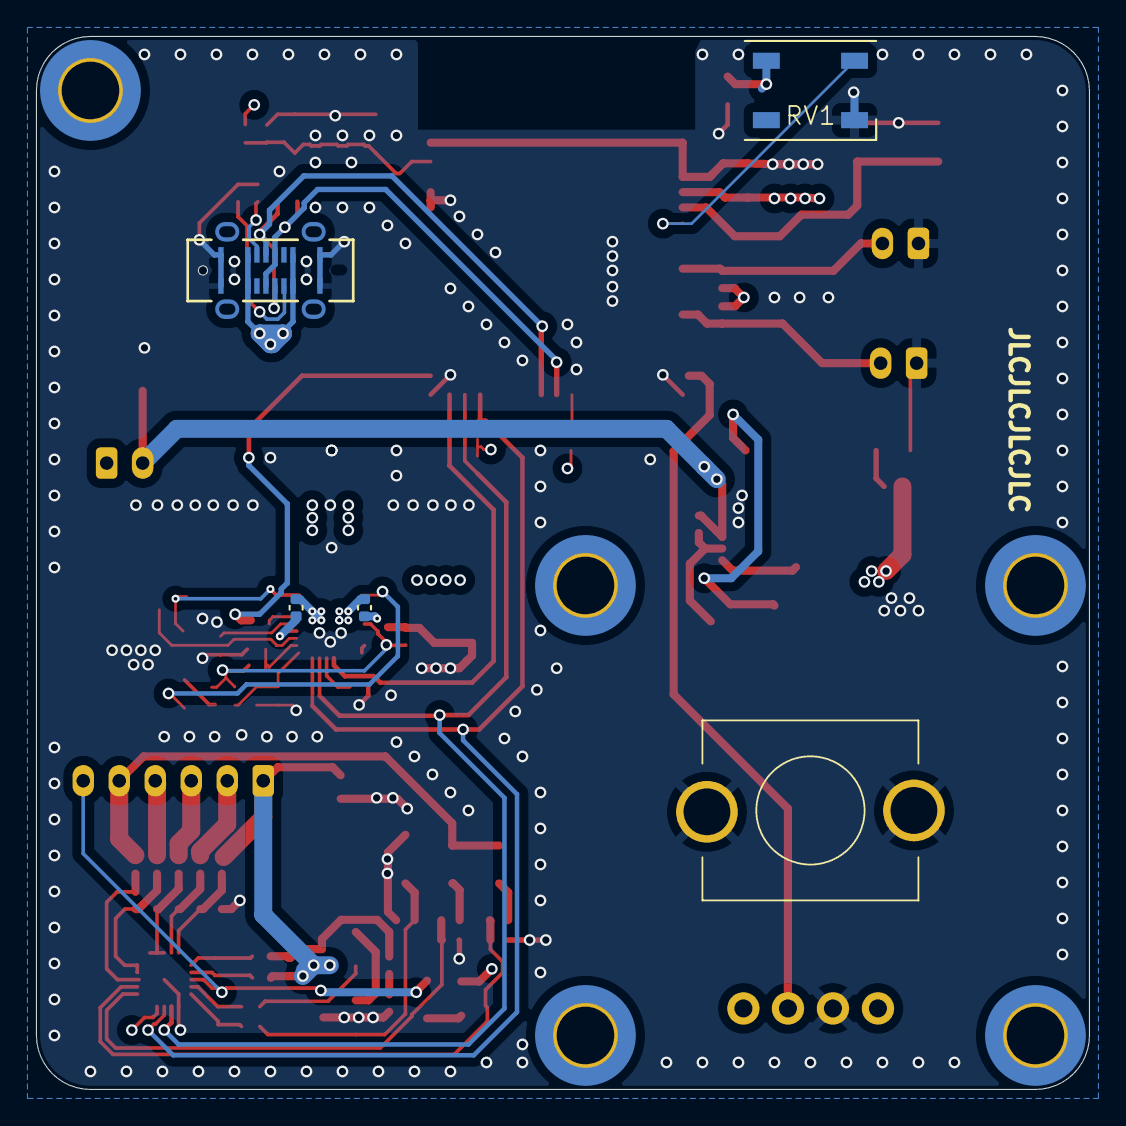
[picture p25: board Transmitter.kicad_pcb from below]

Board: 4 copper layers, 58.5 x 58.5 mm, 111 parts (5 on the bottom side), 65 nets.

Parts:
BQ25792RQMR1: BQ25792
C1, C10, C23, C28, C36, C39, C40: 0.1u; C_0402_1005Metric
C2, C5, C7, C9, C11, C12, C13, C14, C15, C16, C17, C18: 10u; C_0805_2012Metric
C3, C4: 47n; C_0402_1005Metric
C6: .1u; C_0402_1005Metric
C8: 4.7u; C_0402_1005Metric
C20, C29, C37, C38: 1u; C_0402_1005Metric
C21: 1n; C_0402_1005Metric
C24: 10uf; C_0402_1005Metric
C25: 10u; C_0402_1005Metric
C26: 22u; C_0402_1005Metric
C27: 22u; C_0805_2012Metric
C30, C31, C32, C33, C34: 220nf; C_0402_1005Metric
C35: 100p; C_0402_1005Metric
D1: LED; LED_0603_1608Metric
D2: LED; C_0805_2012Metric
D3: EVVOSS16; D_SOD-128
D4: D_Zener; D_SOD-323F
D5: WS2812B; LED_WS2812B_PLCC4_5.0x5.0mm_P3.2mm
D6, D7, D8, D9: 1N4148WQ-13-F; D_SOD-323
D10, D11, D12, D13, D14: TVN3V3B1S; D_0402_1005Metric
H1, H2, H3, H4, H5: MountingHole; MountingHole_3.2mm_M3_DIN965_Pad_TopBottom
J1: USB_C_Receptacle_USB2.0; CONN_GSB1CA11101DSHR_AMP
J2: UP_BTN; JST_PH_B2B-PH-K_1x02_P2.00mm_Vertical
J3: DN_BTN; JST_PH_B2B-PH-K_1x02_P2.00mm_Vertical
J6: JST_PH; JST_PH_B6B-PH-K_1x06_P2.00mm_Vertical
JP1: BQ76905_Bypass; SolderJumper-2_P1.3mm_Open_RoundedPad1.0x1.5mm
L1: 1u; L_1008_2520Metric
Q1: 2N7002; SOT-23
Q12, Q13: NMOS; SOT-23
Q14: PMOS; SOT-23
R1, R2, R16, R20, R22: 10k; R_0402_1005Metric
R3, R4, R5: 5.1k; C_0402_1005Metric
R6, R47, R48: 5.1k; R_0402_1005Metric
R7, R8, R9, R10: 100k; C_0402_1005Metric
R11, R42, R44, R45: 100; R_0402_1005Metric
R12: 127k; R_0402_1005Metric
R13: 5.24k; R_0402_1005Metric
R14: 30.31k; R_0402_1005Metric
R15: 6.04k; R_0402_1005Metric
R17, R49: 100k; R_0402_1005Metric
R18, R19: 10k; C_0402_1005Metric
R37, R38, R39, R40, R41: 10; R_0402_1005Metric
R43: 1m; R_0402_1005Metric
R46: 0; R_0402_1005Metric
RV1: R_Potentiometer; Potentiometer_Bourns_PVT111-3
SW1: Reset; Tactile_5.5mmx2.85mm
SW2: SW_SPST; JST_PH_B2B-PH-K_1x02_P2.00mm_Vertical
SW3: Boot; Tactile_5.5mmx2.85mm
U1, U2: TPS22810DRV; WSON-6-1EP_2x2mm_P0.65mm_EP1x1.6mm
U3: AZ1117-3.3; SOT223
U4: ESP32-S3-MINI-1-N8; XCVR_ESP32-S3-MINI-1-N8
U5: UQFN-20-1EP_3x3mm_P0.4mm_EP1.85x1.85mm

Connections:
+3.3V: C15.1, C26.1, C27.1, C28.1, D5.1 (VDD), Q14.2 (G), R6.1, R7.2, R10.2, R18.1, R19.1, R20.1, R22.1, RV1.1, U3.2 (VO), U4.3 (3V3)
/ADDRS_LED: D5.4 (DIN), U4.5 (IO1)
/BAT+: C14.1, C18.1, C24.1, D4.1 (K), D6.2 (A), D7.2 (A), J6.5, R11.2, R37.1, U2.6 (VIN)
/BATP: BQ25792RQMR1.18 (BATP), R11.1
/BAT_C0: J6.1, JP1.1 (A), R41.1, R42.2, R43.1
/BAT_C1: J6.2, R40.1
/BAT_C2: J6.3, R39.1
/BAT_C3: J6.4, R38.1
/BC_INT: R2.1, U4.31 (IO35)
/BTST1: BQ25792RQMR1.4 (BTST1), C3.1
/BTST2: BQ25792RQMR1.19 (BTST2), C4.2
/CE: BQ25792RQMR1.13 (CE), R1.2
/D+: D12.2 (A2), J1.A6 (D+), J1.B6 (D+), U4.24 (IO20/D+)
/D-: D13.2 (A2), J1.A7 (D-), J1.B7 (D-), U4.23 (IO19/D-)
/DN_BTN: J3.2, R10.1, U4.11 (IO7)
/ESP_EN: C29.1, D11.2 (A2), R20.2, SW1.2, U4.45 (EN)
/ESP_IO0: D10.2 (A2), SW3.2, U4.4 (IO0_BOOT0)
/ILIM_HIZ: BQ25792RQMR1.17 (ILIM_HIZ), R12.1, R17.1
/INT: BQ25792RQMR1.21 (INT), R2.2
/PMID: BQ25792RQMR1.29 (PMID), C6.1, C7.1, C9.1, C11.1
/POT: RV1.2, U4.15 (IO11)
/PROG: BQ25792RQMR1.20 (PROG), R15.1
/QON: BQ25792RQMR1.12 (nQON), U4.30 (IO48)
/REGN: BQ25792RQMR1.5 (REGN), C8.1, R3.1, R12.2, R13.1
/SCL: BQ25792RQMR1.14 (SCL), R19.2, U4.29 (IO34), U5.12 (SCL)
/SDA: BQ25792RQMR1.15 (SDA), R18.2, U4.28 (IO33), U5.13 (SDA)
/SDRV: BQ25792RQMR1.24 (SDRV), C21.1, U2.5 (EN/UVLO)
/STAT: BQ25792RQMR1.1 (STAT), D1.1 (K)
/SW1: BQ25792RQMR1.28 (SW1), C3.2, L1.2
/SW2: BQ25792RQMR1.26 (SW2), C4.1, L1.1
/TS: D8.1 (K), J6.6, U5.8 (TS)
/UP_BTN: J2.2, R7.1, U4.8 (IO4)
/VAC: BQ25792RQMR1.8 (VAC2), BQ25792RQMR1.9 (VAC1)
/VBAT: BQ25792RQMR1.22 (BAT), BQ25792RQMR1.23 (BAT), U2.1 (VOUT)
/VBUS: C16.1, C20.1, C23.1, C25.1, D3.1 (K), U1.1 (VOUT), U3.3 (VI)
/VC0: C33.2, C34.1, R41.2, U5.5 (VC0)
/VC1: C32.2, C33.1, R40.2, U5.4 (VC1)
/VC2: C31.2, C32.1, R39.2, U5.1 (VC3A), U5.2 (VC3B), U5.3 (VC2)
/VC3: C30.2, C31.1, R38.2, U5.19 (VC4A), U5.20 (VC4B)
/VC4: C30.1, R37.2, U5.18 (VC5)
/VSYS: BQ25792RQMR1.25 (SYS), C10.1, C12.1, C13.1, C17.1, SW2.1 (A)
/VUSB: BQ25792RQMR1.2 (VBUS), BQ25792RQMR1.3 (VBUS), C1.1, C2.1, C5.1, D3.2 (A), J1.A4 (VBUS), J1.A9 (VBUS), J1.B4 (VBUS), J1.B9 (VBUS), Q1.1 (G), R8.1
GND: BQ25792RQMR1.10 (ACDRV2), BQ25792RQMR1.11 (ACDRV1), BQ25792RQMR1.27 (GND), C1.2, C2.2, C5.2, C6.2, C7.2, C8.2, C9.2, C10.2, C11.2, C12.2, C13.2, C14.2, C15.2, C16.2, C17.2, C18.2, C20.2, C21.2, C23.2, C24.2, C25.2, C26.2, C27.2, C28.2, C29.2, C34.2, C37.2, C38.2, C40.2, D2.1 (K), D4.2 (A), D5.3 (VSS), D9.2 (A), D10.1 (A1), D11.1 (A1), D12.1 (A1), D13.1 (A1), D14.2 (A2), J1.A1 (GND), J1.A12 (GND), J1.B1 (GND), J1.B12 (GND), J2.1, J3.1, JP1.2 (B), Q1.2 (S), Q13.3 (S), R1.1, R4.2, R5.2, R8.2, R14.2, R15.2, R16.2, R17.2, R49.1, RV1.3, SW1.1, SW3.1, U1.4 (GND), U1.7 (GND), U2.4 (GND), U2.7 (GND), U3.1 (GND), U3.4 (GND), U4.1 (GND), U4.2 (GND), U4.42 (GND), U4.43 (GND), U4.46 (GND), U4.47 (GND), U4.48 (GND), U4.49 (GND), U4.50 (GND), U4.51 (GND), U4.52 (GND), U4.53 (GND), U4.54 (GND), U4.55 (GND), U4.56 (GND), U4.57 (GND), U4.58 (GND), U4.59 (GND), U4.60 (GND), U4.61 (EXP), U4.62 (GND), U4.63 (GND), U4.64 (GND), U4.65 (GND), U5.11 (VSS), U5.21 (VSS)
unnamed: BQ25792RQMR1.16 (TS), R13.2, R14.1, R16.1
unnamed: C39.2, C40.1
unnamed: D1.2 (A), R3.2
unnamed: D2.2 (A), R6.2
unnamed: D6.1 (K), R44.1
unnamed: D7.1 (K), R46.1
unnamed: D8.2 (A), Q14.1 (D)
unnamed: D9.1 (K), Q13.2 (G), R48.2, R49.2
unnamed: D14.1 (A1), R9.2, SW2.2 (B), U1.6 (VIN)
unnamed: J1.A5 (CC1), R4.1
unnamed: J1.B5 (CC2), R5.1
unnamed: Q1.3 (D), R9.1, U1.5 (EN/UVLO)
unnamed: Q12.1 (D), Q13.1 (D)
unnamed: Q12.2 (G), R47.2
unnamed: C39.1, Q12.3 (S), R43.2, R45.2
unnamed: R22.2, U4.22 (IO18/DAC2)
unnamed: C37.1, R44.2, U5.17 (BAT)
unnamed: R48.1, U5.10 (CHG)
unnamed: R47.1, U5.9 (DSG)
unnamed: C38.1, R46.2, U5.16 (REGSRC)
unnamed: C35.1, C36.1, R42.1, U5.7 (SRN)
unnamed: C35.2, C36.2, R45.1, U5.6 (SRP)

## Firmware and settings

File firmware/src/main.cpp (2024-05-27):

#include <Arduino.h>
#include "WiFi.h"
#include "ESPmDNS.h"
#include <ArduinoOTA.h>
#include "config.h"
#include <WebServer.h>
#include "web_controller.h"
#include "esp_wifi.h"
#include "wifi_credentials.h"
#include "gpio.h"
#include "WifiDebug.h"
#include "OTA.h"
#include "scripts.h"
#include "styles.h"
#include "battery.h"

WebServer server(80);

void handle_root();
void  handle_js();
void handle_css();
void handle_battery();
void setup()
{
  gpio::init_common_gpio();  

  

  if(MAKE_AP){
    WiFi.mode(WIFI_AP);
    WiFi.softAP("WeldConnect", NULL);
  }else{
    WiFi.begin(ssid, password);
    int32_t start_time = millis();
    
    while(WiFi.status() != WL_CONNECTED){
      delay(100);
      digitalWrite(gpio::STATUS_LED, (int)(millis()/100)%2);
    }
    //Serial.println("Wifi Connected");
  }
  DEBUG_BEGIN(115200);
  esp_wifi_set_max_tx_power(8);
  int8_t tx_power;
  esp_wifi_get_max_tx_power(&tx_power);

  activateWifiBootloader();

  server.on("/", handle_root);
  server.on("/scripts.js", handle_js);
  server.on("/styles.css", handle_css);
  server.on("/battery.html", handle_battery);
  server.begin();
  // IPAddress ip = WiFi.localIP();
  // DEBUG_PRINTF("%s", ip.toString());

  // if(!MDNS.begin("weldconnect")){
  //   while(1){
  //     digitalWrite(gpio::STATUS_LED, (int)(millis()/100)%2);
  //   }
  // }
}

void loop()
{
  server.handleClient();
  digitalWrite(13, (int)(millis()/1000)%2);
  ota_loop();
}

// Handle root url (/)
void handle_root() {
  DEBUG_PRINT("Sending HTML page");
  server.send_P(200, "text/html", web_controller);
}

void handle_js(){
  DEBUG_PRINT("Got reuest for js");
  server.send_P(200, "text/js", scripts);
}

void handle_css(){
  DEBUG_PRINT("Got request for css");
  server.send_P(200, "text/css", styles);
}

void handle_battery(){
  DEBUG_PRINT("Got request for battery.html");
  server.send_P(200, "text/html", battery);
}

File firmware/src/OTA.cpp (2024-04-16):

#include "OTA.h"

void activateWifiBootloader()
{
  ArduinoOTA.setHostname("Welder_Controller");

  ArduinoOTA
      .onStart([]()
               {
      String type;
      if (ArduinoOTA.getCommand() == U_FLASH)
        type = "sketch";
      else // U_SPIFFS
        type = "filesystem";

      // NOTE: if updating SPIFFS this would be the place to unmount SPIFFS using SPIFFS.end()
       })
      .onEnd([]()
             {  })
      .onProgress([](unsigned int progress, unsigned int total)
                  {  })
      .onError([](ota_error_t error)
               {
      Serial.printf("Error[%u]: ", error);
       });

  ArduinoOTA.begin();
}

void ota_loop(){
    ArduinoOTA.handle();
}

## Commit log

2024-03-12 Completed Power Path
    [Transmitter.kicad_pcb, Transmitter.kicad_sch, Welder_Knob.kicad_sch]
2024-03-13 Completed Transmitter Schematic
    [Transmitter.kicad_sch]
2024-03-16 Transmitter PCB complete
    [Transmitter.kicad_sch, Transmitter.step]
2024-03-17 Finished Receiver Schematic
    [Receiver.kicad_pcb, Receiver.kicad_sch]
2024-03-17 Completed Receiver PCB
    [Receiver.kicad_pcb, Receiver.kicad_sch]
2024-03-18 Removed old files
    [Receiver.kicad_pcb, Receiver.kicad_sch, Transmitter.kicad_pcb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]
2024-03-19 Revision 1.2 of receiver board
    [Receiver-B_Cu.gbr, Receiver-B_Mask.gbr, Receiver-B_Paste.gbr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]
2024-03-19 Begin bom
2024-03-19 Add bms to schematic
    [Receiver.kicad_sch]
2024-03-21 BMS added to hardware
    [Receiver.kicad_pcb, Receiver.kicad_sch, Transmitter.kicad_pcb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]
2024-03-22 update costs and finalize dxf for laser cutting
    [Main Plate.dxf, Receiver Side Plate.dxf]
2024-03-23 updates to bom cost
2024-03-25 working upload on esp32s3
2024-03-25 working custom board
2024-03-26 rename battery leads, update footprints
    [Receiver.csv, Receiver.kicad_pcb, Receiver.kicad_sch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]
2024-03-27 update mcu to ESP32S3
2024-03-27 Add board definition
2024-03-29 change CDC mode to allow Serial printing
2024-03-30 add torsion spring
2024-04-03 Add cell balancing
    [Receiver.kicad_sch]
2024-04-04 add battery balancing IC
    [Receiver.kicad_pcb, Receiver.kicad_sch]
2024-04-05 add battery balancing to transmitter
    [Transmitter.kicad_pcb, Transmitter.kicad_sch]
2024-04-06 update readme details
    [Receiver.kicad_sch]
2024-04-06 add bom link
2024-04-12 update battery display
2024-04-12 add battery levels
2024-04-13 add tvs diodes
    [Receiver.kicad_pcb, Receiver.kicad_sch]
2024-04-16 add stitching vias
    [Receiver.kicad_pcb]
2024-04-17 update emc
    [Receiver.kicad_pcb, Transmitter.kicad_pcb]
2024-04-26 create bom
    [Receiver.csv, Receiver.kicad_pcb, Transmitter.csv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]
2024-05-27 PCB revision
    [Receiver.kicad_pcb, Receiver.kicad_sch, Transmitter.kicad_pcb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]
